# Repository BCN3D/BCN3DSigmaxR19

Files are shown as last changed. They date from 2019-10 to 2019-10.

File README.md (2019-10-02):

## What’s hold in this repository?
This repository will hold all the information about the Mechanics of the BCN3D Sigmax R19.
As a declared Open Source organization, it's in our mission to release all the original design files to you to be able to learn, reuse and improve. Open Source not only means code, it also concerns hardware.

We’ve managed to design and manufacture the BCN3D Sigmax R19 thanks to our previous experience in the 3D printing industry, the ideas coming from the community, our engineering background and a narrow collaboration with our suppliers. Our goal is justify the decisions we took and share the know-how we acquired so far.

We also provide the source files for those who want to check the core of the BCN3D Sigmax R19. You can consult both the CAD files and the technical drawings.

## CONCEPT DESIGN
During the concept design stage we set a clear target which determined the whole design and decisions: The BCN3D Sigmax R19 is a professional printer.

### Aesthetics
It has to look  like a professional equipment. Our previous printers were made with aluminium extruded profiles and plastic printed parts. That made sense for printers oriented to makers or schools, sold as a kit. But, in this case, aesthetic was a major player. For this reason, we adopted a welded aluminium frame, which allows the Sigmax to be a unique and attractive 3D printer

### Multimaterial
As a professional printer, it has to print as many materials as possible. Not only for engineers, who require tough -or flexible-, functional polymers, but also for designers who need the aesthetic component. However, material is not the only limitation. Complex geometries, overhangs and 3D printing doesn’t get along. So we wanted the Sigmax to be a real solution for those users who need to print with supports as a must. In conclusion, the Sigmax is the first and only commercial 3D printer with an Independent Dual Extuder (IDEX) system, which avoid all the side problems dual extrusion may cause.

### High Quality
The 3D Printing industry is maturing. Users are more and more demanding and 3D printing must be a solution, not a headache. For this reason, the Sigmax has to be a reliable piece of engineering, easy to assemble, maintain and capable to print seamlessly high quality objects, no matter how complex they are.

### High Capacity
Real-life and functional parts are not always small. A big printing volume is a great advantage for a professional 3D Printer although the Sigmax intends to be a desktop-sized printer. Allocating all the items and devices inside the frame, while granting ease-to-use and optimizing the axes structure were a key goal.

## DETAIL DESIGN INSIGHTS

We faced dozens of challenges during the design process. Below we describe some of them:

### Frame
Probably the biggest challenge. First we thought in a chassis made of profiles and then cover it. But then realized the cost in materials for that solution would be high enough to look for alternatives that could contribute more in the aesthetic field, even that could be a bit more expensive. On the other side, we wanted the Sigmax to be an accessible printer, wide and open in order to ease the handling and operation. So we decided to explore the option of designing a unibody frame where all the mechanical components were mounted on and with a wide frontal oberture.

First we had to decide between using aluminium or steel. Steel offers many advantages: It’s a very stiff metal, great to build structures and precise mechanical systems. In addition, it’s easy to work with and cheap. But it’s -really- heavy. We contemplated the option of using a thinner metal sheet of steel for the frame. After ordering a prototype, we dismissed the idea, though. Still it had a great mechanical behaviour and a relative low weight, the feeling of touching a thin metal sheet (1.5mm) was unpleasant because it felt like a cutting edge. And it didn’t look sturdy. So to achieve both a reliable look and a pleasant contact, we needed to go up to 3mm thickness. But then the shipping costs would be absurdly high and the handling, a constant hassle -both during the assembly process and for the final user.

Aluminium, on the other hand, provides lightness and a smooth and sturdy look. But it’s more expensive as a material and it’s harder to laser cut and weld. After balancing pros and cons, we bet on aluminium option -although we had a plan B.

The second big issue to manage was the manufacturing process. We contemplated two different ways to do it: either manufacture the frame by parts and screw them all together in the assembly line or weld the frame. Welding aluminium is hard and the welding process itself has some thermal and geometric implications that have to be considered. But it allows to reduce the assembling time dramatically while it outsources a key process.

As alternative, designing the frame as separate parts to screw together was considerably cheaper - as you save a handmade process such as welding and polishing. But the assembling of the frame and adjustment could be very delicate and incompatible with our production tag time. So the overall cost wouldn’t be that different in both options. The aesthetic component, though, would be very penalized with this alternative, because we would need to add dozens of screws on the frame.

For these reasons, we finally opted for a welded structure. We sat hours with our supplier discussing the best way to design every single part in order to grant a proper alignment between the faces that would hold the axes. Furthermore, we also studied the mechanical behaviour of the frame with some CAE studies, simulating stress and deformations during a standard usage.

### High quality components
A good frame is not enough to achieve amazing results. In such a precision equipment as the Sigmax, all the mechanical components play a key role. Due to the product requirements in terms of size and use of the internal space of the printer we had, we opted for a axes structure with the toolheads moving in the XY plane and an up and down moving Z axis.

With the XY plane decided to mount high precision linear guides. Despite its cost slightly higher than a system based on rods and bearings, the linear rails offer a professional look, an easy assembling and a compact package.

Regarding the Z axis, we were aware of the importance to have a robust guide system in order to avoid classic artifacts in printed parts related with a bad Z performance, such as Z wobbling. We also had experience using couplings and to connect the actuator with the leadscrew and we knew that a bad assembling could cause poor quality results. With this background, we chose using Ø12mm guide rods and a stepper motor with an inserted leadscrew. The whole system provides a high repeatability and accuracy.

### Independent Dual Extrusion
A 3D printer with such an specific feature increases the design unknowns and multiplies the components. Not only the firmware and the electronics need to be highly customized, but also mechanically there are some decisions to take.

First of all, because of the multiple components to hold, the internal parts tend to be more complex than other printers. So we decided to use aluminium sheet bending technology to manufacture the inner parts. As the manufacturing tolerances are acceptable for the purposes we intend and the technology is cheap and easily scalable, we considered the technology optimum.  

Two independent Extruders means have an extra moving stepper for the second toolhead, and the extra toolhead itself. On the other hand, when printing with both extruders it’s important to have a bucket to purge the idle hotends before start printing the model again. All this parts add weight to a moving element, which is a problem to print fast because the high inertias may worsen the print quality. So we designed the X and Y Axis as light as possible, saving as many grams as possible with every single component. Not only weight is important when doubling the toolheads, but also space. So we decided to adopt a bowden-based feeding system and miniaturize all the items as much as possible.

### Big Printing Volume
The BCN3D Sigmax R19 features 420x297x210mm printing volume. In order to provide such a big volume and a free space on both sides to park the idle toolhead, but still having a desktop-sized printer, we had to reorient the Z platform. The main issue to solve, though, was granting the stiffness of the structure with a big overhang of more than 300mm.

To prevent vibrations, we adopted high quality bearings with low clearance and we designed and  simulated a custom metal sheet structure, which allows to get a great quality prints with a smooth surface despite the big overhang.

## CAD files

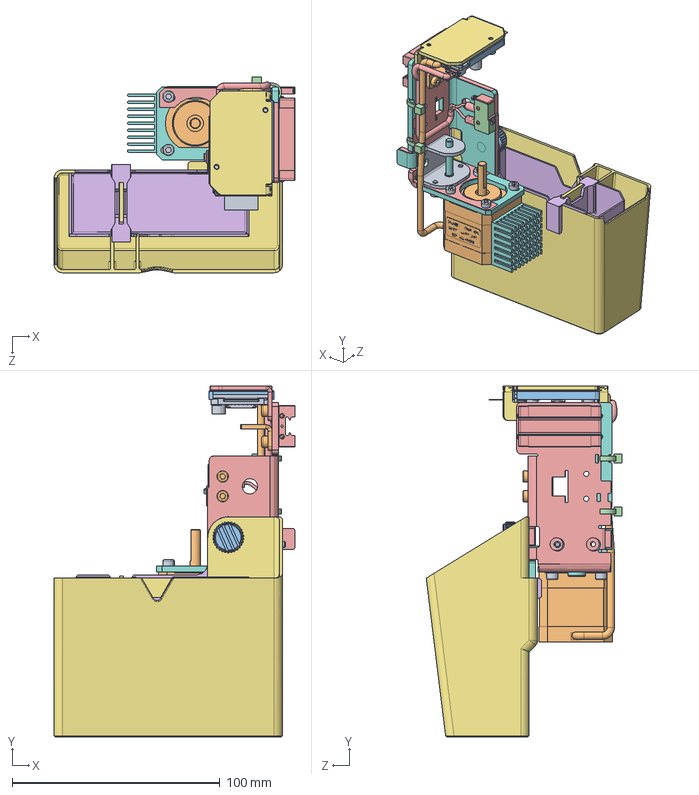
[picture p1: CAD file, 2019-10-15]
CAD/SW/BCN3DSigma-M05C02.0P000 X Axis Right.SLDASM
116.0 x 169.0 x 94.2 mm
DIN912 M3x6 x 8
DIN912 M3x8 x 6
DIN125 M3 poliamida x 2
DIN125 M3 x 2
10850-B00_Purger base right
040M05C02.0P04B X Stepper Driver Holder Right
BCN3DSigma-M02C01.0P10A Idler pulley shaft
BCN3DSigma-M04C00.0P03F Stepper Driver Board
10901-A00_Nema 14
BCN3DSigma-M05C01.0P08Z Purger Button
BCN3DSigma-M09C00.0P20A Zip tie x 2
Linear guide slide
Sigma_R17-M05C01.0P14D Cloth Support
BCN3DSigma-M05C01.0P07C Silicone Cloth
10828-A00_Stepper Holder Right
10830-B01_X Axis Idler
BCN3DSigma-M05C01.0P01D Belt Clamp
BCN3DSigma-M05C01.0P11F Driver spacer
BCN3DSigma-M02C01.0P08Z Endstop
BCN3DSigma-M09C00.0P15A Endstop X Right
BCN3DSigma-M04C00.0P09A Drivers Heatsink
040M05C01.0P017Z Heatsink 28x28x15

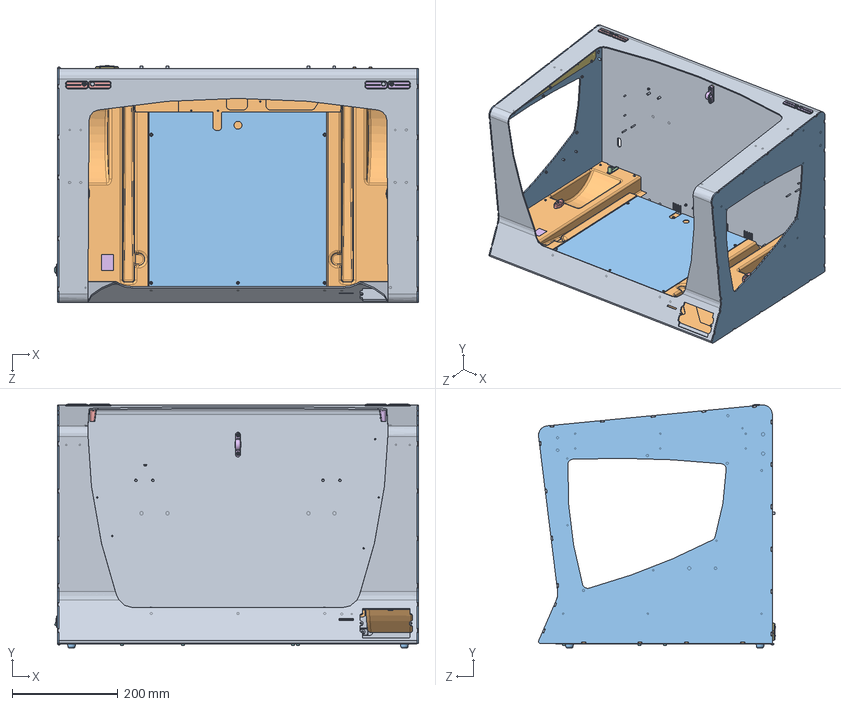
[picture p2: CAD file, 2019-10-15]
CAD/SW/040M01C00.0P000 Structure.SLDASM
686.9 x 459.6 x 447.2 mm
040M01C01.0P01K (RiT - Reverse Engineered) Top frame
040M01C01.0P02E (Test) Bottom frame
BCN3DSigma-M01C01.0P03D (Test) Left_Right side x 2
BCN3DSigma-M01C01.0P05D Y Idler Tensioner x 2
BCN3DSigma-M01C01.0P29H Bowden exit Left
BCN3DSigma-M01C01.0P29H Bowden exit Right
BCN3DSigma-M01C01.0P07G (Test) Guide spacer x 2
040M01C01.0P11Z Power button
040M01C01.0P12Z USB Extension Cable
040M01C01.0P15A Square 90 x 8
040M01C01.0P16A Square 60 x 3
BCN3DSigma-M01C01.0P30C Curve flat cable holder x 2
BCN3DSigma-M01C01.0P20C Front LED connector clamp x 2
BCN3DSigma-M01C01.0P22D Plain flat cable holder x 4
040M04C00.0P07Z Power Entry Filter
040M01C01.0P17Z Fusible
DIN7982 M3.5x13 x 2
A3DIN912 M3x10 x 6
A3DIN125 M3 poliamida x 14
A3DIN934 M3 x 48
A3DIN985 M3 x 9
040M02C01.0P14A DRY-RUNNING MOUNTED SLEEVE BRNG
040M02C01.0P15C Y Axis Pillow Bearing Spacer
A3DIN7981 3.2x9.5 x 6
A3ISO7380 M3x10 x 11
040M01C02.0P01E Inner cover
BCN3DSigma-M01C02.0P06D Bowden entry guide x 2
BCN3DSigma-M01C02.P07F Bowden entry x 2
040M01C02.0P09A Crush Label
10924-A00_Coupling collet x 2
A3DIN912 M3x6 x 7
A3DIN125 M3 x 4
14062-A00_Bottom cover
040M01C03.0P02Z Leg x 4

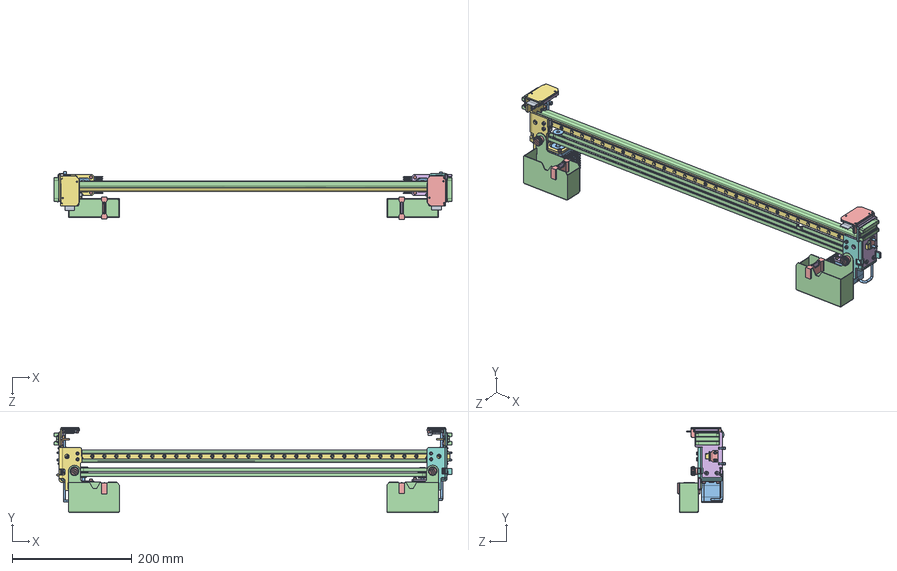
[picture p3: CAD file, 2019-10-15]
CAD/SW/040M05C00.0P000 X Axis.SLDASM
663.4 x 142.0 x 79.4 mm
BCN3DSigma-M02C01.0P15Z GT2 Pulley Ø4 Bearing Bore 6 Runice x 2
BCN3DSigma-M02C01.0P016Z Spacer 4x8x6 Essentra x 2
BCN3DSigma-M05C01.0P15Z GT2 Pulley Ø5 Bore 6 Runice x 2
040M05C00.0P01Z X Belt x 2
DIN912 M3x6 x 16
DIN912 M3x8 x 12
DIN912 M3x10 x 2
DIN125 M3 poliamida x 4
DIN125 M3 x 4
10831-A00_Belt Clamp
10901-A00_Nema 14 x 2
10849-B00_Purger base left
BCN3DSigma-M05C01.0P08Z Purger Button x 2
BCN3DSigma-M05C01.0P11F Driver spacer x 2
BCN3DSigma-M05C01.0P12B X Stepper Driver Holder Left
BCN3DSigma-M02C01.0P10A Idler pulley shaft x 2
BCN3DSigma-M04C00.0P03F Stepper Driver Board x 2
BCN3DSigma-M09C00.0P15A Endstop X Left
BCN3DSigma-M09C00.0P20A Zip tie x 4
Linear guide slide x 2
Sigma_R17-M05C01.0P14D Cloth Support x 2
BCN3DSigma-M05C01.0P07C Silicone Cloth x 2
10028-A00_Stepper Holder Left
10830-B01_X Axis Idler x 2
BCN3DSigma-M02C01.0P08Z Endstop x 2
BCN3DSigma-M04C00.0P09A Drivers Heatsink x 2
040M05C01.0P017Z Heatsink 28x28x15 x 2
10850-B00_Purger base right
040M05C02.0P04B X Stepper Driver Holder Right
10828-A00_Stepper Holder Right
BCN3DSigma-M05C01.0P01D Belt Clamp
BCN3DSigma-M09C00.0P15A Endstop X Right
A3DIN912 M3x6 x 4
A3DIN912 M3x10 x 4
A3DIN912 M3x8 x 6
14060-A00_X Reinforcement x 2
BCN3DSigma-M05C03.0P02G X Support x 2
10847-A01_connection plate x 3
14068-A00_X Guide

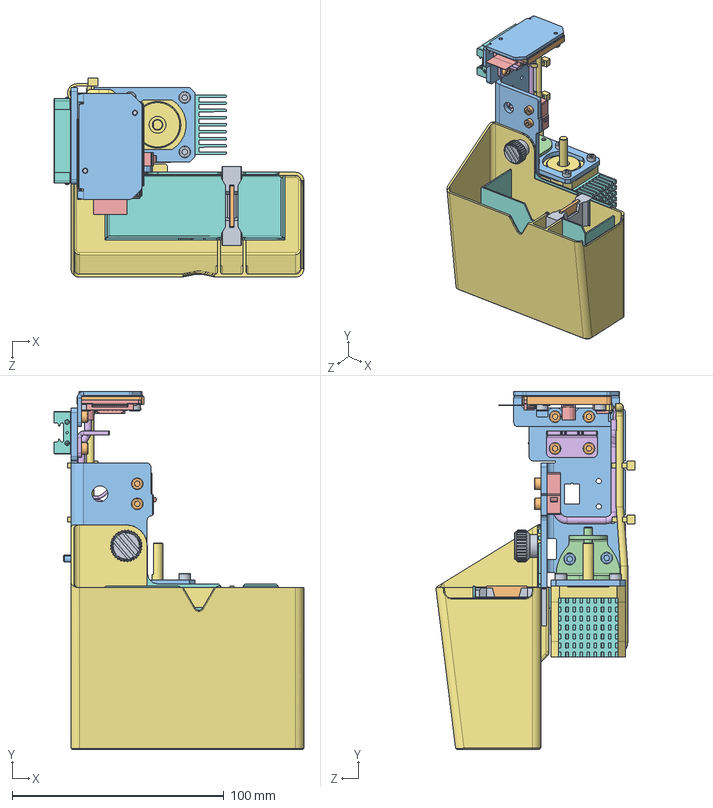
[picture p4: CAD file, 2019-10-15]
CAD/SW/BCN3DSigma-M05C01.0P000 X Axis Left.SLDASM
118.0 x 169.0 x 94.2 mm
DIN912 M3x6 x 8
DIN912 M3x8 x 6
DIN912 M3x10 x 2
DIN125 M3 poliamida x 2
DIN125 M3 x 2
10831-A00_Belt Clamp
10901-A00_Nema 14
10849-B00_Purger base left
BCN3DSigma-M05C01.0P08Z Purger Button
BCN3DSigma-M05C01.0P11F Driver spacer
BCN3DSigma-M05C01.0P12B X Stepper Driver Holder Left
BCN3DSigma-M02C01.0P10A Idler pulley shaft
BCN3DSigma-M04C00.0P03F Stepper Driver Board
BCN3DSigma-M09C00.0P15A Endstop X Left
BCN3DSigma-M09C00.0P20A Zip tie x 2
Linear guide slide
Sigma_R17-M05C01.0P14D Cloth Support
BCN3DSigma-M05C01.0P07C Silicone Cloth
10028-A00_Stepper Holder Left
10830-B01_X Axis Idler
BCN3DSigma-M02C01.0P08Z Endstop
BCN3DSigma-M04C00.0P09A Drivers Heatsink
040M05C01.0P017Z Heatsink 28x28x15

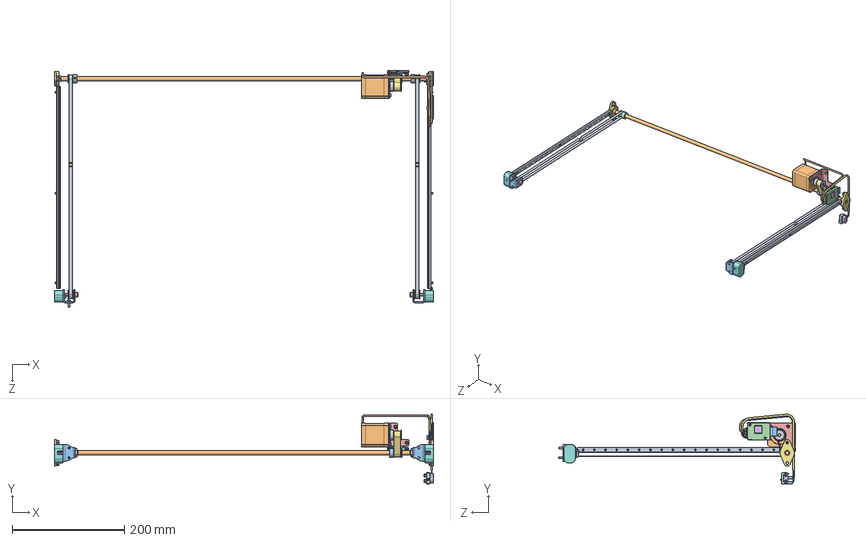
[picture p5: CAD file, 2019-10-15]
CAD/SW/040M02C00.0P000 Y Axis.SLDASM
675.5 x 124.6 x 421.8 mm
A3DIN985 M2.5 x 2
A3DIN912 M3x6 x 6
A3DIN912 M3x10 x 11
A3DIN913 M3x3 x 4
A3DIN934 M5 x 4
A3DIN913 M4x3 x 4
040M02C01.0P01Z Bearing Pillow Block x 2
BCN3DSigma-M02C01.0P02E Idler Spacer x 2
040M02C01.0P03Z Y Guide x 2
14065-A00_Transmission Bar
10838_A01-Y Axis Idler x 2
040M02C01.0P08Z Endstop
BCN3DSigma-M02C01.0P10A Idler pulley shaft x 2
BCN3DSigma-M02C01.0P12A Y Endstop spacer
040M09C00.0P14B Y Endstop cable
040M09C00.0P21A Enstop shrink tube x 2
040M02C01.0P09Z Y Belt x 2
BCN3DSigma-M02C01.0P15Z GT2 Pulley Ø4 Bearing Bore 6 Runice x 2
10883-A00_Pulley Ø8 Bore 12 Runice
10885-A00_GT2 Pulley Ø8 Bore 6 Runice x 2
A3DIN934 M3 x 6
A3DIN 913 M3x10 x 2
A3DIN125 M3 poliamida x 2
040M02C02.0P02C Y Belt tensor
040M02C02.0P04Z GT2 Pulley Ø5mm Bore 12mm width
040M02C02.0P06Z Nema17 47mm
040M04C00.0P03F Stepper Driver Board
BCN3DSigma-M05C01.0P11F Driver spacer
040M02C02.0P01D Y Stepper Holder
Drivers Heatsink
040M02C00.0P01Z Y Main Belt

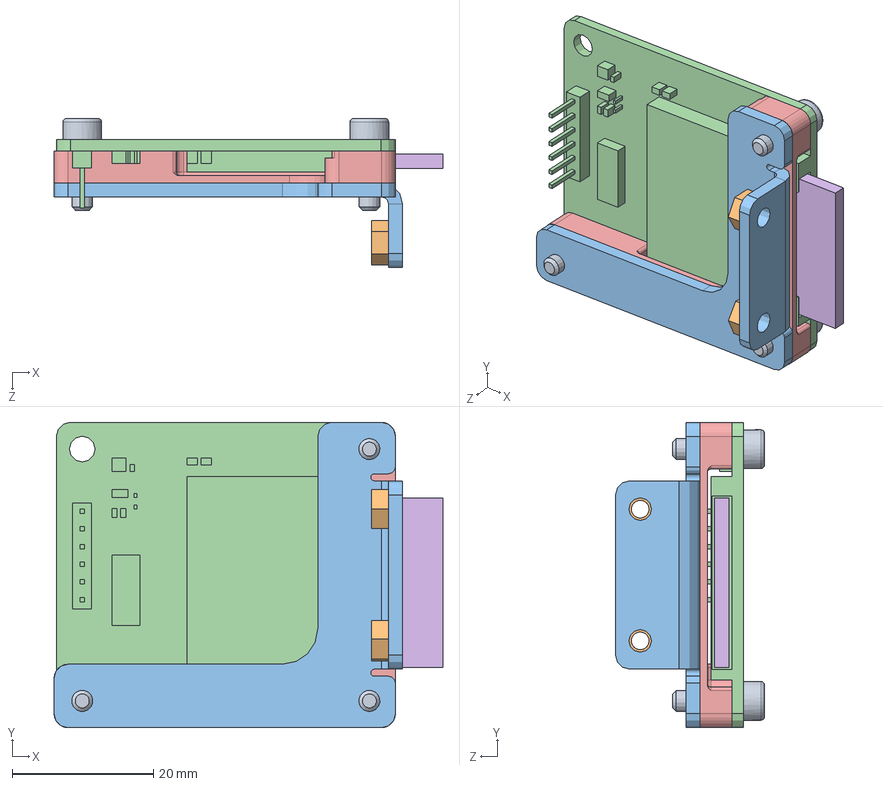
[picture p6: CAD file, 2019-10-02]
CAD/SW/040M04C02.0P000 SD Unit.SLDASM
55.1 x 43.2 x 21.1 mm
A3DIN912 M3x10 x 3
A3DIN934 M3 x 2
040M04C02.0P01D SD Holder
BCN3DSigma-M04C02.0P02AA SD module
040M04C02.0P03A SD spacer
040M04C02.0P04Z SD Card 8GB

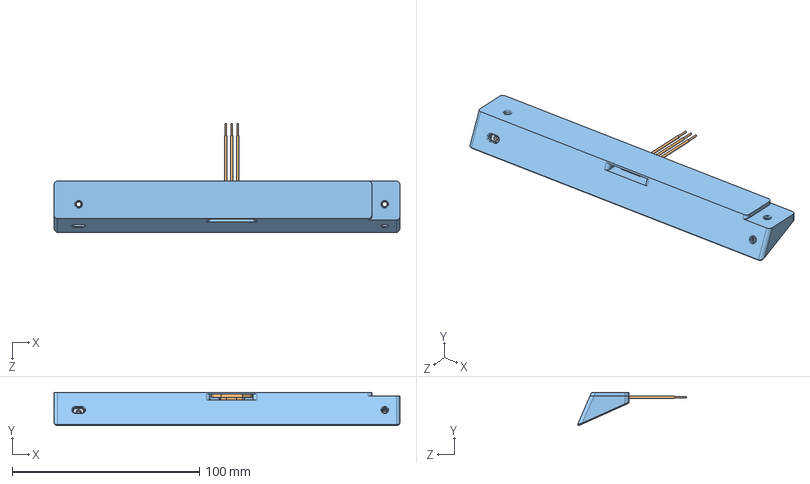
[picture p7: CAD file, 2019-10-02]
CAD/SW/040M01C04P000 HES Mount.SLDASM
185.0 x 17.9 x 58.2 mm
DIN934 M3 x 4
NPN Hall Effect Sensor (RS=765-9325)
040M01C04P002B Sensor Mount

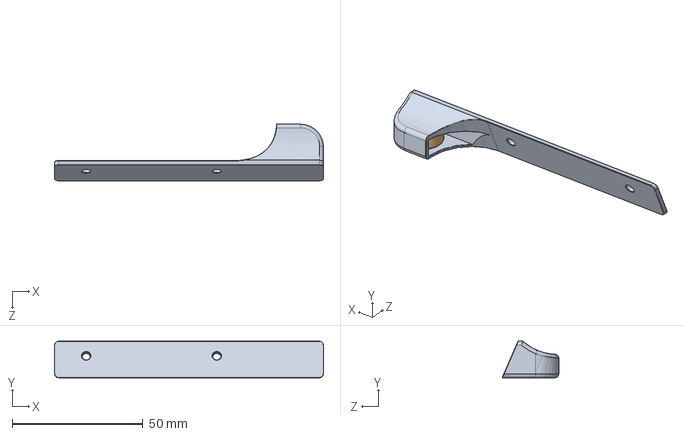
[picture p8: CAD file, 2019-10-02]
CAD/SW/040M01C04P001 HES Trigger.SLDASM
103.0 x 14.0 x 21.7 mm
040M01C04P003E Magnet Holder
Magnet (Supermagnete = R-15-06-06-N)

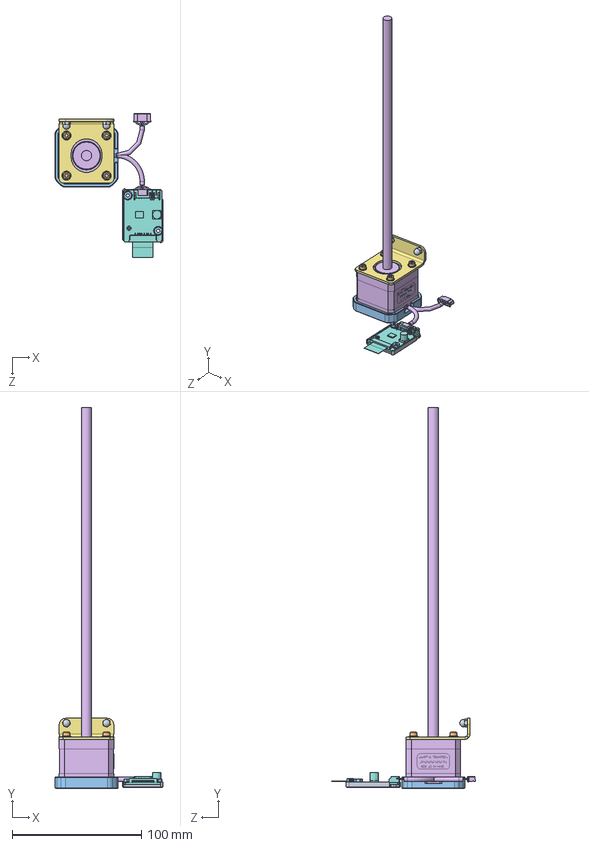
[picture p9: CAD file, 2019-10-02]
CAD/SW/040M03C03.0P000 Z Motor.SLDASM
83.6 x 294.5 x 111.5 mm
A3DIN1587 M3 x 2
A3DIN912 M3x10 x 4
A3DIN934 M3 x 2
A3DIN125 M3 x 4
A3DIN125 M3 poliamida x 2
040M03C03.0P01Z Z Motor
BCN3DSigma-M03C03.0P02C Z Stepper Holder
040M04C00.0P03F Stepper Driver Board
BCN3DSigma-M05C01.0P11F Driver spacer
Drivers Heatsink
Z Motor Rest Support^040M03C03.0P000 Z Motor

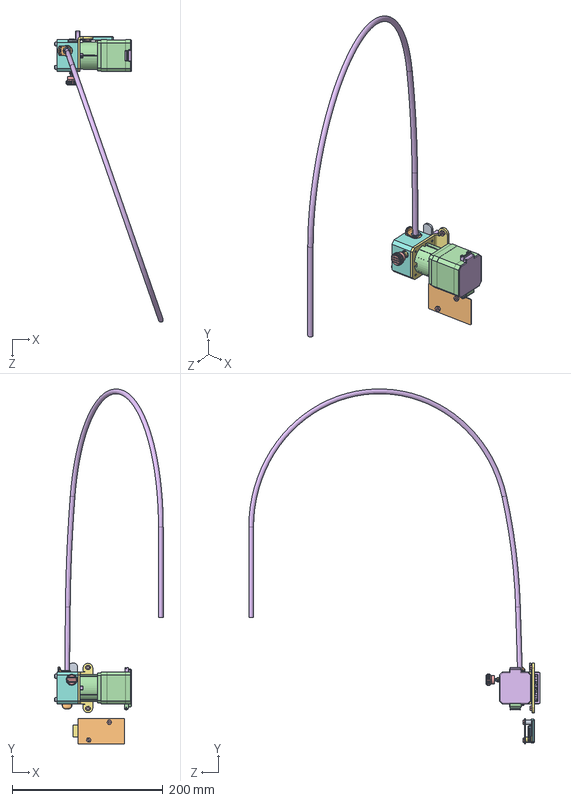
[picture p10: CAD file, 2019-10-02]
CAD/SW/040M07C01.0P000C Left extruder.SLDASM
143.8 x 470.5 x 386.3 mm
A3DIN912 M3x30 x 3
A3DIN913 M3x3
DIN931 M4x50 (91280A154)
A3DIN912 M3x8 x 3
A3DIN934 M3 x 4
040M07C01.0P29B (Test) Separador Drive Gear
040M04C00.0P03F Stepper Driver Board
BCN3DSigma-M05C01.0P11F Driver spacer
Separador nylon negre 3.2x6x8 x 2
040M07C01.0P06C Extruder driver cover
PHR-6_PRUEBA x 2
040M07C01.0P10AA Nema 17 40mm
040M07C01.0P25Z Driving Gear
040M07C01.0P24Z Driven Gear
040M07C01.0P05E Extruder Stepper Holder
040M07C01.0P026E Extruder Body Left
040M07C01.0P027B Extruder Tensor Left
040M07C01.0P04D Pneufit coupling x 2
040M07C01.0P19Z Coupling collet x 2
040M07C01.0P029Z Pin
040M05C01.0P08Z Purger Button
040M07C01.0P07B Bowden tube
040M07C01.0P13A Extruder spring
Drivers Heatsink
filament
BCN3DSigma-M07C01.0P14D Coupling Clip x 2

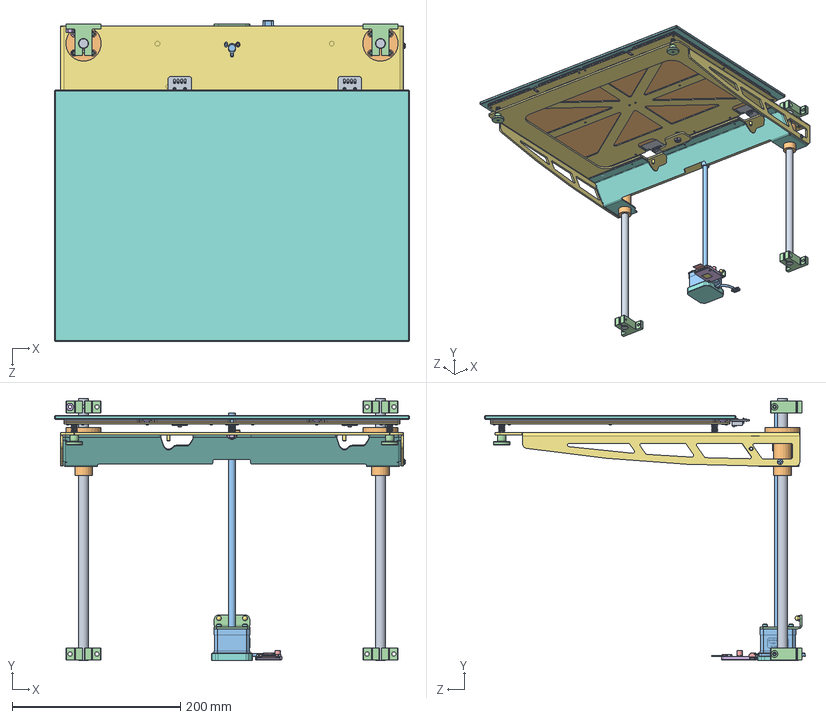
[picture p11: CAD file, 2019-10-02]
CAD/SW/040M03C00.0P000 Z axis.SLDASM
422.0 x 312.0 x 381.5 mm
040M03C01.0P01G Lower platform
040M03C01.0P02E Reinforcement
040M03C01.0P03B Z Bar x 2
040M03C01.0P04Z Flanged Linear Bushing x 2
040M03C01.0P06Z Shaft Support x 4
A3DIN7991 M3x6 x 18
A3DIN985 M5
040M03C02.0P01D Upper platform
14066-A00_Glass
040M03C02.0P05E Heated bed x 2
040M03C02.0P03C Cork x 2
040M03C02.0P04Z Printing surface spring x 3
040M03C02.0P07Z Bed Thumbscrew x 2
040M03C02.0P09A Thumbscrew Label x 2
040M03C02.0P06Z Magnet x 4
A3DIN1587 M3 x 2
A3DIN912 M3x10 x 4
A3DIN934 M3 x 2
A3DIN125 M3 x 4
A3DIN125 M3 poliamida x 2
040M03C03.0P01Z Z Motor
BCN3DSigma-M03C03.0P02C Z Stepper Holder
040M04C00.0P03F Stepper Driver Board
BCN3DSigma-M05C01.0P11F Driver spacer
Drivers Heatsink
Z Motor Rest Support^040M03C03.0P000 Z Motor

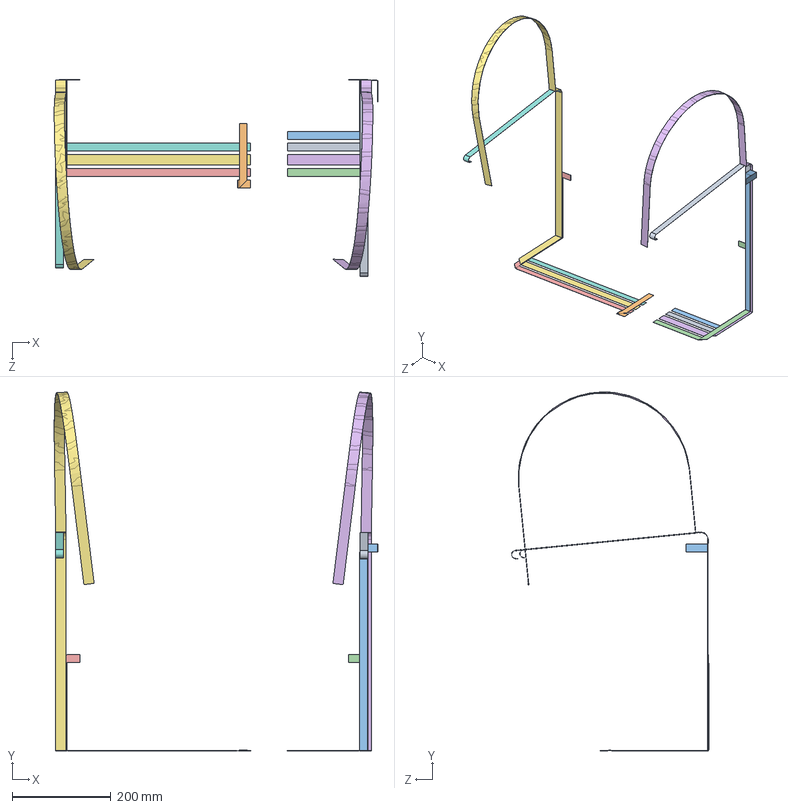
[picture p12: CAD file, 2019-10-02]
CAD/SW/040M09C00.0P000 Wiring.SLDASM
656.3 x 728.0 x 399.5 mm
040M09C00.0P01A FFC X1 stepper
040M09C00.0P03A FFC Z stepper
040M09C00.0P04A FFC Y stepper
040M09C00.0P05A FFC Extruder 1
040M09C00.0P06B FFC Extruder 0
040M09C00.0P08B FFC Hotend 1
040M09C00.0P07C FFC Hotend 0
040M09C00.0P02B FFC X0 stepper

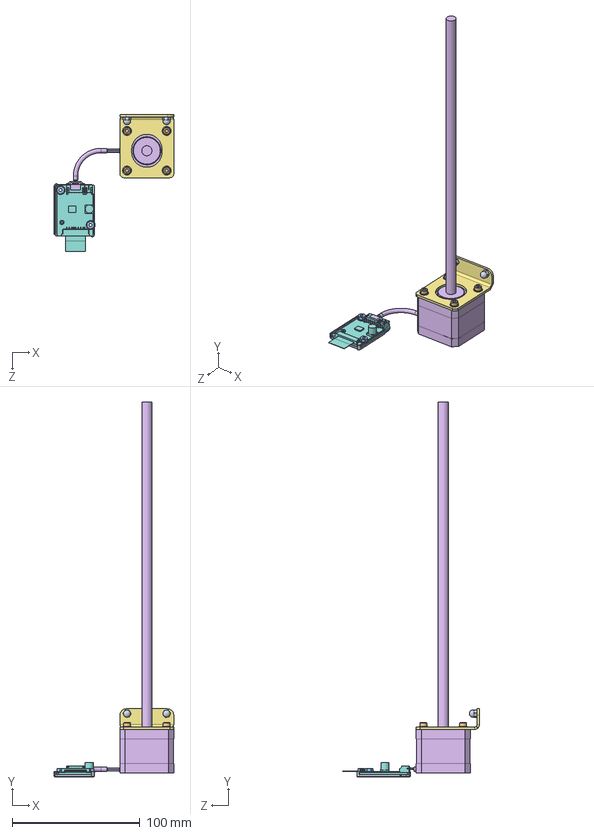
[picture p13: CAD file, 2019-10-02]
CAD/SW/BCN3DSigma-M03C03.0P000 Z Motor.SLDASM
93.8 x 293.6 x 107.2 mm
DIN1587 M3 x 2
DIN912 M3x10 x 4
DIN934 M3 x 2
DIN125 M3 x 4
DIN125 M3 poliamida x 2
10903-A00 Z Motor
10983-A00_Z Stepper Holder
BCN3DSigma-M04C00.0P03F Stepper Driver Board
BCN3DSigma-M05C01.0P11F Driver spacer
BCN3DSigma-M04C00.0P09A Drivers Heatsink

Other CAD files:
CAD/SW/040M07C04.0P000 Filament Runout Sensor.SLDASM
CAD/SW/040M04C01.0P02A Cable mainboard to adapator lcd.sldasm
CAD/SW/040M07C03.0P000 Bifurcation.sldasm
CAD/SW/040M05C01.0P000 X Axis Left.SLDASM
CAD/SW/040M09C00.0P17B Relay to mainboard cable.sldasm
CAD/SW/040M01C01.0P11Z Power button.SLDPRT
CAD/SW/040M01C01.0P12Z USB Extension Cable.SLDPRT
CAD/SW/040M01C01.0P15A Square 90.SLDPRT
CAD/SW/040M01C01.0P16A Square 60.SLDPRT
CAD/SW/040M01C01.0P17Z Fusible.SLDPRT
CAD/SW/040M01C02.0P000 Structure covers.SLDASM
CAD/SW/040M01C02.0P01E Inner cover.SLDPRT
CAD/SW/040M01C02.0P05F Extruder entry bowden.SLDPRT
CAD/SW/040M01C02.0P09A Crush Label.SLDPRT
CAD/SW/040M01C03.0P000 Bottom cover.SLDASM
CAD/SW/040M01C03.0P02Z Leg.SLDPRT
CAD/SW/040M01C04P002B Sensor Mount.SLDPRT
CAD/SW/040M01C04P003E Magnet Holder.SLDPRT
CAD/SW/040M02C01.0P14A DRY-RUNNING MOUNTED SLEEVE BRNG.SLDPRT
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

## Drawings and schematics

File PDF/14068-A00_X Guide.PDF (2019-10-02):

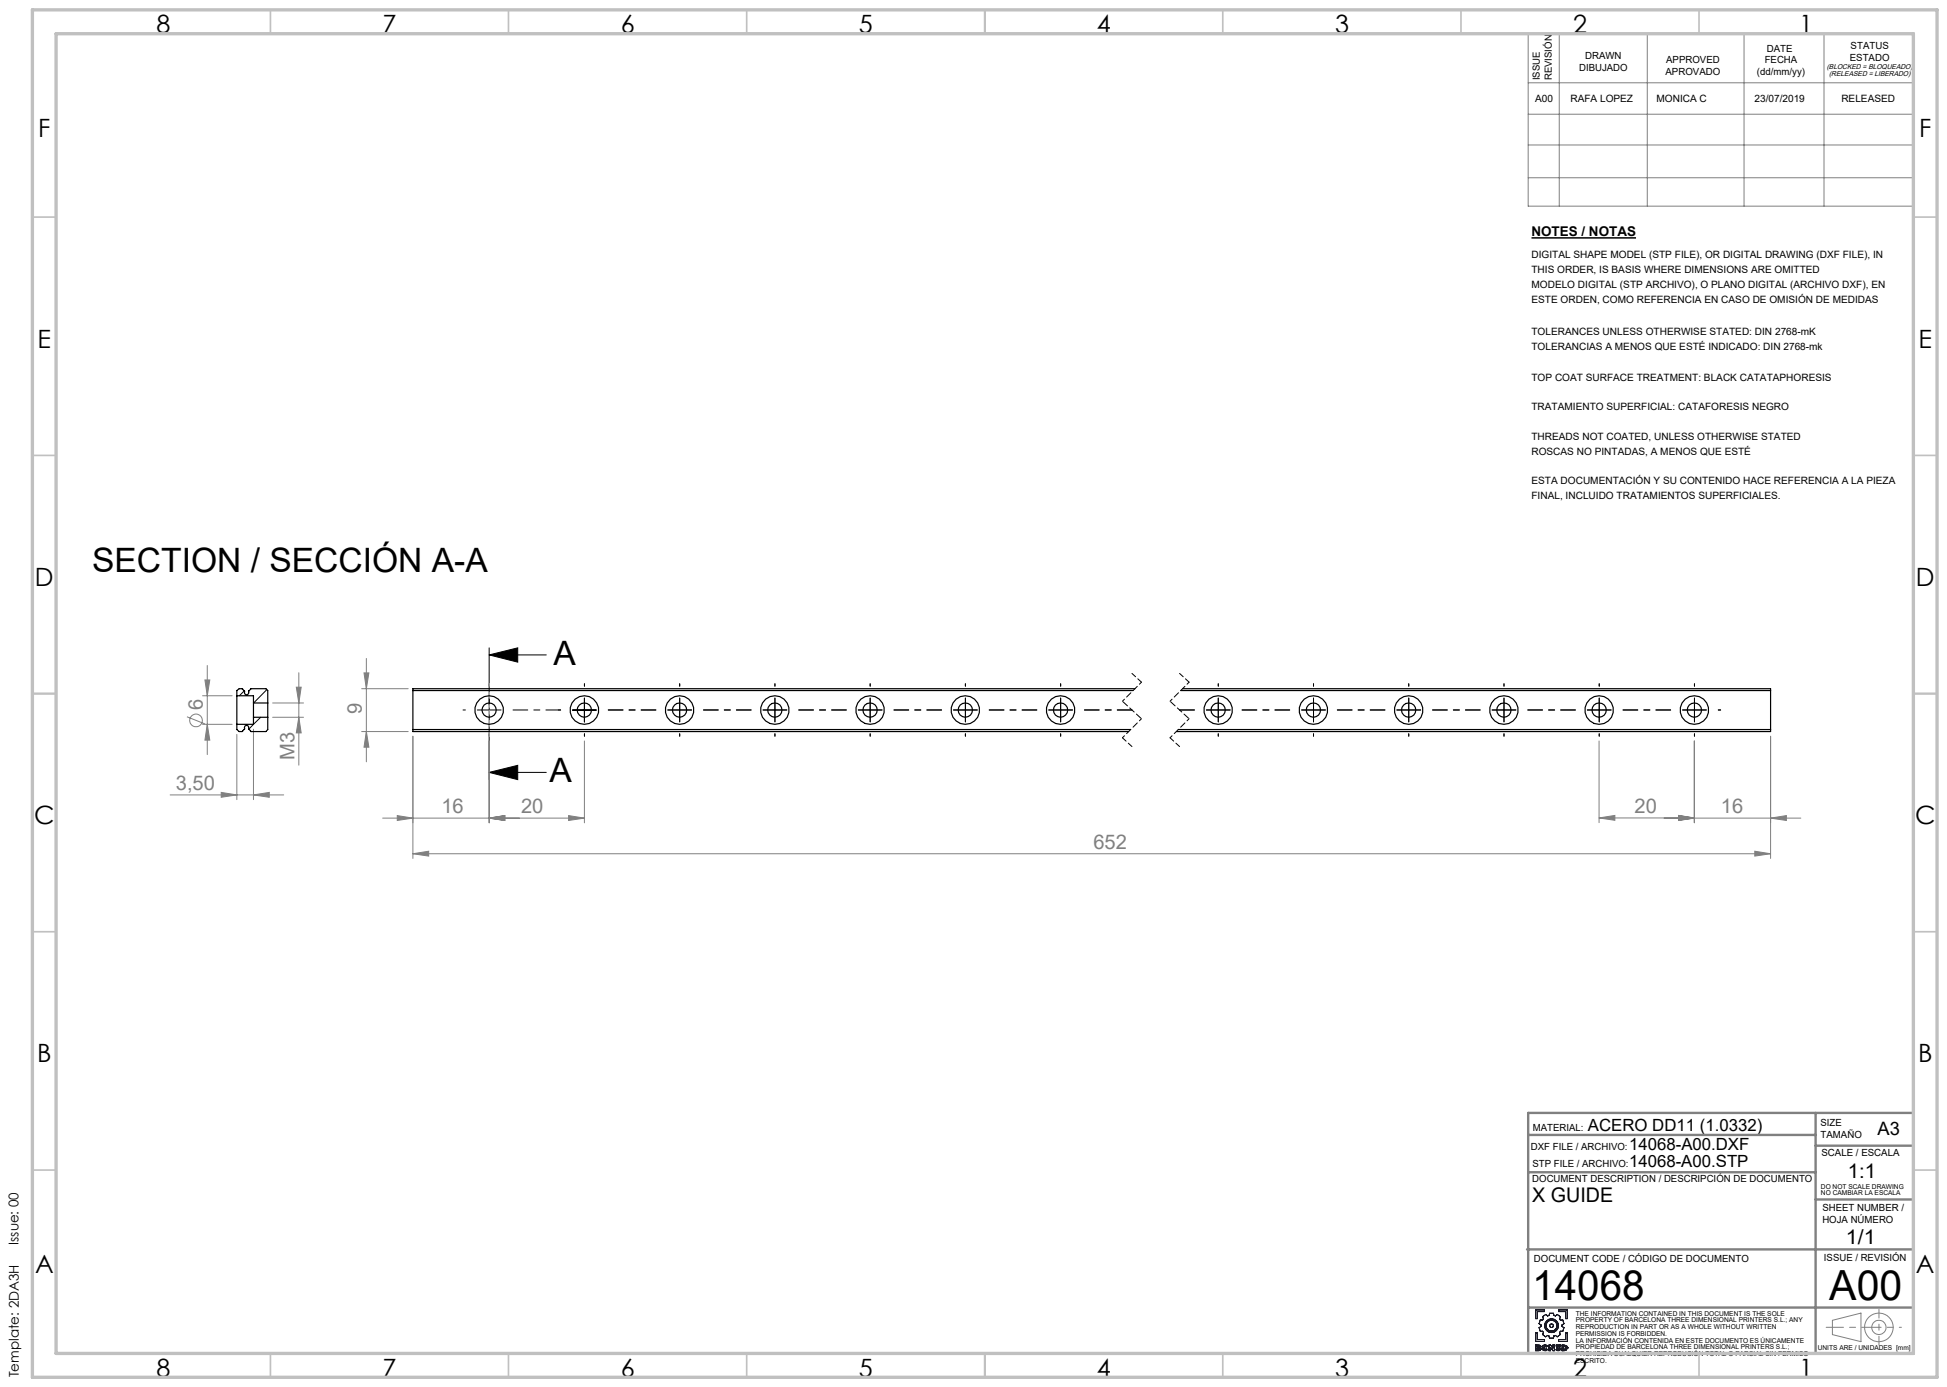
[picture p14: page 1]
SCALE / ESCALA; NOTES / NOTAS; SECTION / SECCIÓN A-A; Template: 2DA3H Issue: 00; ACERO DD11 (1.0332)

DRAWN DIBUJADO | APPROVED APROVADO | DATE FECHA (dd/mm/yy) | STATUS ESTADO (BLOCKED = BLOQUEADO) (RELEASED = LIBERADO)

A00 | RAFA LOPEZ | MONICA C | 23/07/2019 | RELEASED

DIGITAL SHAPE MODEL (STP FILE), OR DIGITAL DRAWING (DXF FILE), IN
THIS ORDER, IS BASIS WHERE DIMENSIONS ARE OMITTED
MODELO DIGITAL (STP ARCHIVO), O PLANO DIGITAL (ARCHIVO DXF), EN
ESTE ORDEN, COMO REFERENCIA EN CASO DE OMISIÓN DE MEDIDAS

TOLERANCES UNLESS OTHERWISE STATED: DIN 2768-mK
TOLERANCIAS A MENOS QUE ESTÉ INDICADO: DIN 2768-mk

TOP COAT SURFACE TREATMENT: BLACK CATATAPHORESIS

TRATAMIENTO SUPERFICIAL: CATAFORESIS NEGRO

THREADS NOT COATED, UNLESS OTHERWISE STATED
ROSCAS NO PINTADAS, A MENOS QUE ESTÉ

ESTA DOCUMENTACIÓN Y SU CONTENIDO HACE REFERENCIA A LA PIEZA
FINAL, INCLUIDO TRATAMIENTOS SUPERFICIALES.

MATERIAL:
DXF FILE / ARCHIVO:
STP FILE / ARCHIVO:
DOCUMENT DESCRIPTION / DESCRIPCIÓN DE DOCUMENTO
X GUIDE

DO NOT SCALE DRAWING
NO CAMBIAR LA ESCALA
SHEET NUMBER /
HOJA NÚMERO

DOCUMENT CODE / CÓDIGO DE DOCUMENTO 14068 | ISSUE / REVISIÓN A00

THE INFORMATION CONTAINED IN THIS DOCUMENT IS THE SOLE PROPERTY OF BARCELONA THREE DIMENSIONAL PRINTERS S.L.; ANY REPRODUCTION IN PART OR AS A WHOLE WITHOUT WRITTEN PERMISSION IS FORBIDDEN. LA INFORMACIÓN CONTENIDA EN ESTE DOCUMENTO ES ÚNICAMENTE PROPIEDAD DE BARCELONA THREE DIMENSIONAL PRINTERS S.L.; | UNITS ARE / UNIDADES [mm]

PROHIBIDA CUALQUIER REPRODUCIÓN TOTAL O PARCIAL SIN PERMISO
ESCRITO.

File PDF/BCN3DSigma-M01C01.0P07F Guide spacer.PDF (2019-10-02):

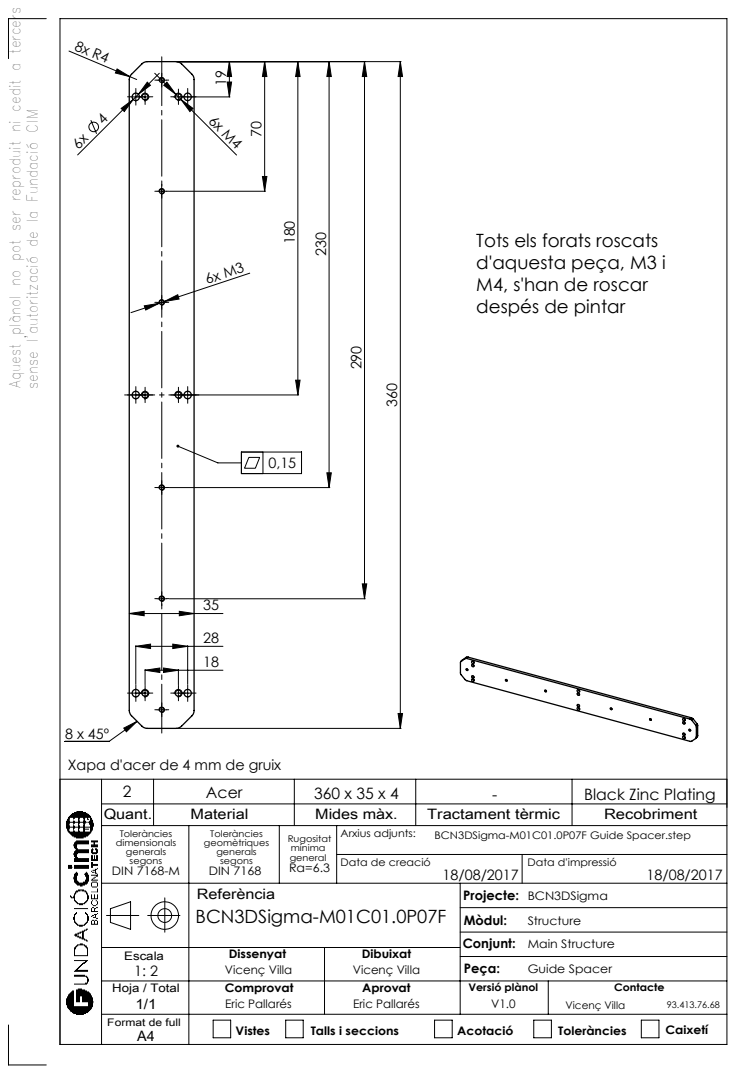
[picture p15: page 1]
Mides màx.; Tractament tèrmic; Recobriment; Data de creació; Data d'impressió; Vistes; Talls i seccions; Acotació; Toleràncies; Caixetí; Guide Spacer

Aquest plànol no pot ser reproduit ni cedit a tercers

sense l'autorització de la Fundació CIM

Tots els forats roscats
d'aquesta peça, M3 i
M4, s'han de roscar
despés de pintar

Xapa d'acer de 4 mm de gruix
Quant.

- Black Zinc Plating

Toleràncies dimensionals generals segons DIN 7168-M | Toleràncies geomètriques generals segons DIN 7168 | Rugositat mínima general Ra=6.3 | Arxius adjunts: BCN3DSigma-M01C01.0P07F Guide Spacer.step

Referència BCN3DSigma-M01C01.0P07F | Projecte: BCN3DSigma Mòdul: Structure Conjunt: Main Structure

Escala 1: 2 | Dissenyat Vicenç Villa | Dibuixat Vicenç Villa

Hoja / Total 1/1 | Comprovat Eric Pallarés | Aprovat Eric Pallarés | Versió plànol V1.0 | Contacte Vicenç Villa 93.413.76.68

Format de full A4

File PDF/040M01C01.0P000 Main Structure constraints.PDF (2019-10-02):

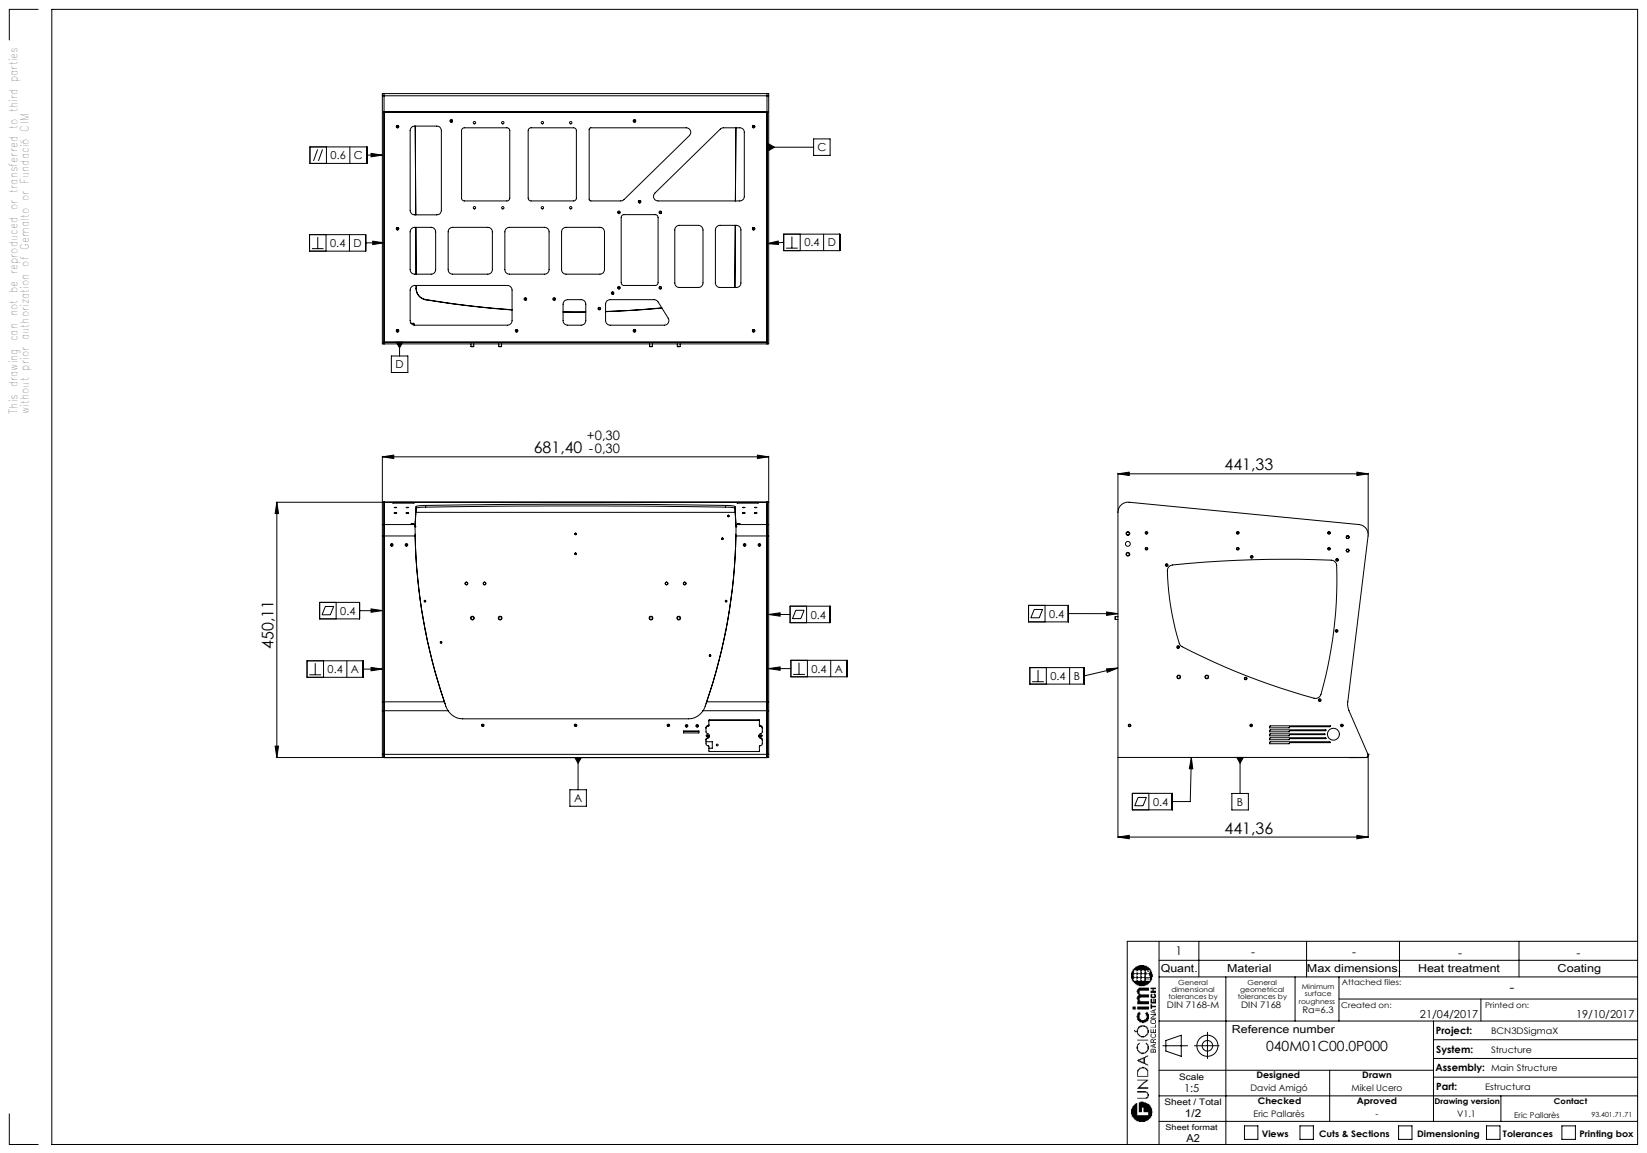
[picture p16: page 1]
Max dimensions.; Heat treatment; Coating; Created on:; Printed on:; Views; Cuts & Sections; Dimensioning; Tolerances; Printing box

This drawing can not be reproduced or transferred to third parties without prior authorization of Gemalto or Fundació CIM

General dimensional tolerances by DIN 7168-M | General geometrical tolerances by DIN 7168 | Minimum surface roughness Ra=6.3 | Attached files: | -

Reference number 040M01C00.0P000 | Project: BCN3DSigmaX System: Structure Assembly: Main Structure

Scale 1:5 | Designed David Amigó | Drawn Mikel Ucero

Sheet / Total 1/2 | Checked Eric Pallarès | Aproved - | Drawing version V1.1 | Contact Eric Pallarès 93.401.71.71

Sheet format A2

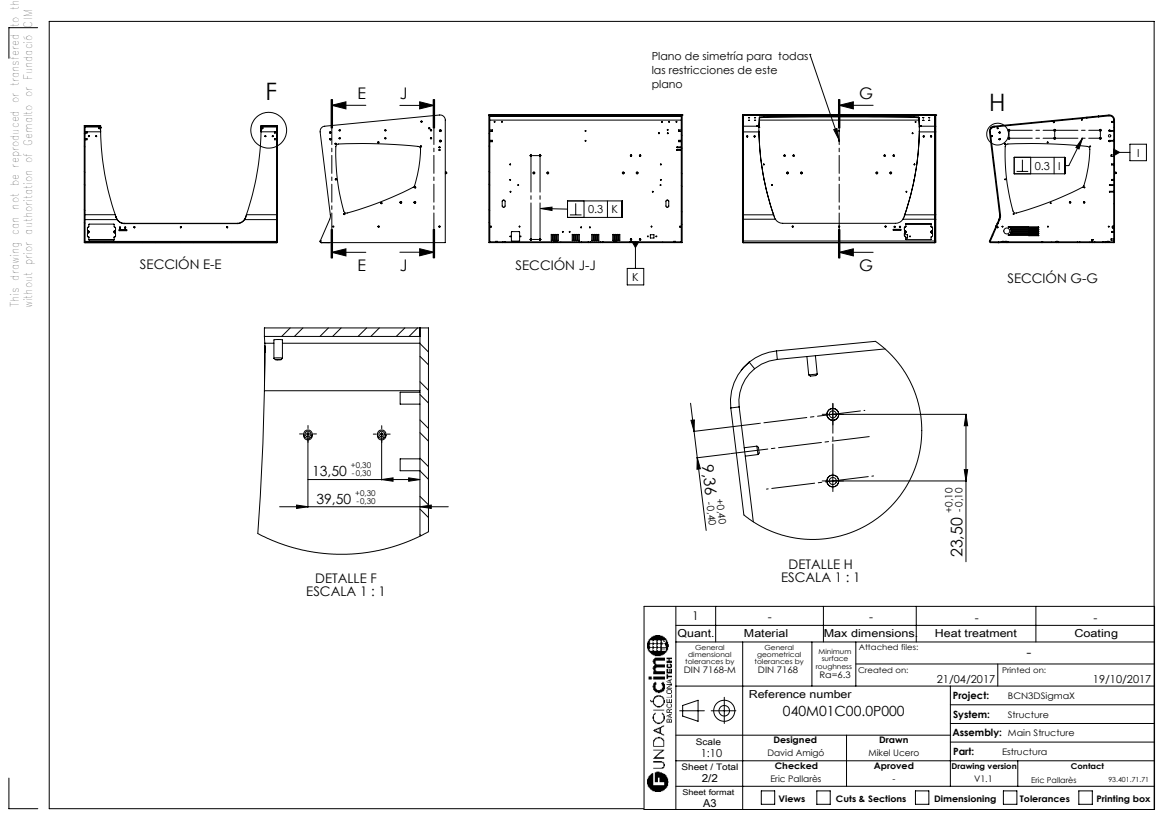
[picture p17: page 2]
Max dimensions.; Heat treatment; Coating; Created on:; Printed on:; Views; Cuts & Sections; Dimensioning; Tolerances; Printing box; SECCIÓN G-G; DETALLE H ESCALA 1 : 1; SECCIÓN E-E; DETALLE F ESCALA 1 : 1; SECCIÓN J-J

This drawing can not be reproduced or transfered to third parts

without prior authoritation of Gemalto or Fundació CIM

Plano de simetría para todas
las restricciones de este
plano

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

Reference number 040M01C00.0P000 | Project: BCN3DSigmaX System: Structure Assembly: Main Structure

Scale 1:10 | Designed David Amigó | Drawn Mikel Ucero

Sheet / Total 2/2 | Checked Eric Pallarès | Aproved - | Drawing version V1.1 | Contact Eric Pallarès 93.401.71.71

Sheet format A3

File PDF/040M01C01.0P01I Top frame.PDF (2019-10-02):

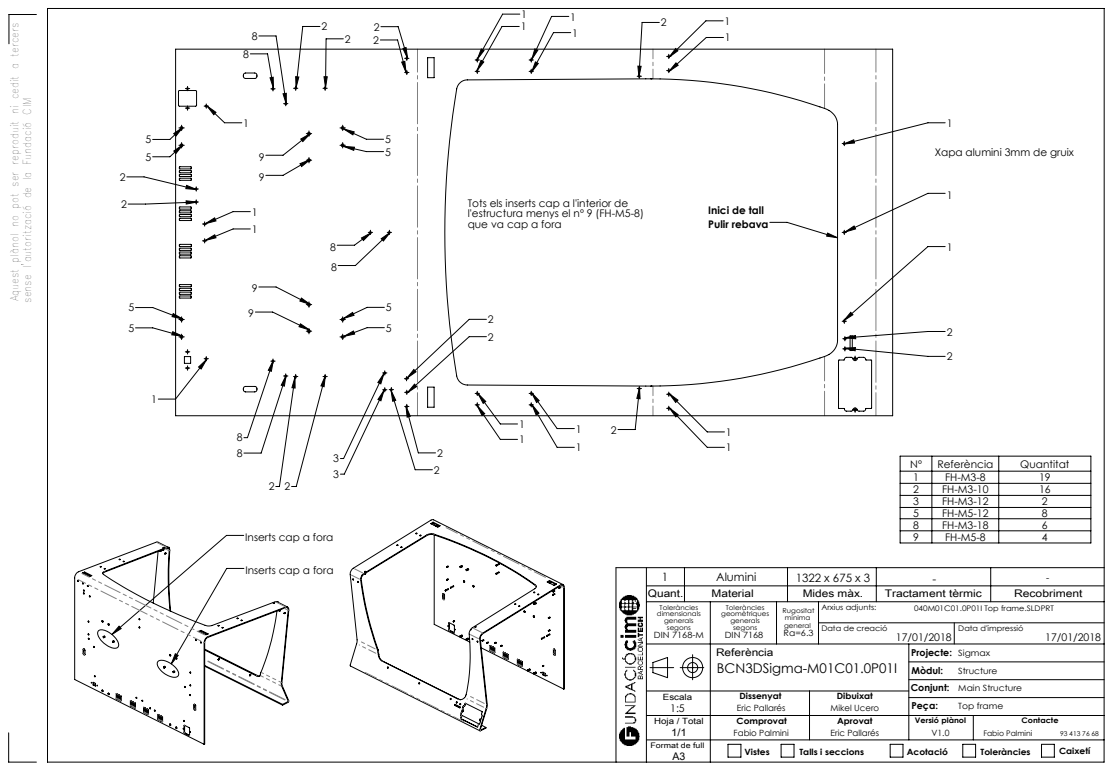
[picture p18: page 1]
Mides màx.; Tractament tèrmic; Recobriment; Data de creació; Data d'impressió; Vistes; Talls i seccions; Acotació; Toleràncies; Caixetí; Top frame; Referència; Quantitat 1

Aquest plànol no pot ser reproduit ni cedit a tercers

sense l'autorització de la Fundació CIM

Xapa alumini 3mm de gruix

Tots els inserts cap a l'interior de
l'estructura menys el nº 9 (FH-M5-8)
que va cap a fora

Inici de tall
Pulir rebava

Inserts cap a fora

Toleràncies dimensionals generals segons DIN 7168-M | Toleràncies geomètriques generals segons DIN 7168 | Rugositat mínima general Ra=6.3 | Arxius adjunts: 040M01C01.0P01I Top frame.SLDPRT

Referència BCN3DSigma-M01C01.0P01I | Projecte: Sigmax Mòdul: Structure Conjunt: Main Structure

Escala 1:5 | Dissenyat Eric Pallarés | Dibuixat Mikel Ucero

Hoja / Total 1/1 | Comprovat Fabio Palmini | Aprovat Eric Pallarés | Versió plànol V1.0 | Contacte Fabio Palmini 93 413 76 68

Format de full A3

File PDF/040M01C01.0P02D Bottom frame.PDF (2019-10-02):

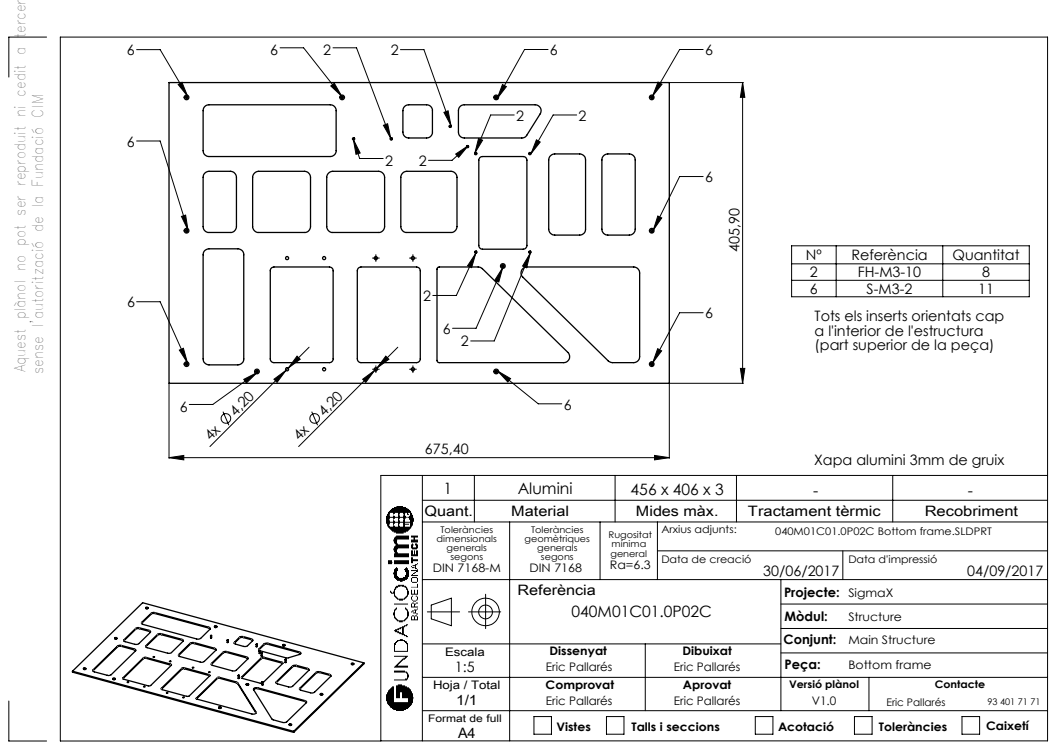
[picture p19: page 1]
Mides màx.; Tractament tèrmic; Recobriment; Data de creació; Data d'impressió; Vistes; Talls i seccions; Acotació; Toleràncies; Caixetí; Bottom frame

Aquest plànol no pot ser reproduit ni cedit a tercers

sense l'autorització de la Fundació CIM

Nº | Referència | Quantitat
2 | FH-M3-10 | 8
6 | S-M3-2 | 11

Tots els inserts orientats cap
a l'interior de l'estructura
(part superior de la peça)

Xapa alumini 3mm de gruix

Toleràncies dimensionals generals segons DIN 7168-M | Toleràncies geomètriques generals segons DIN 7168 | Rugositat mínima general Ra=6.3 | Arxius adjunts: 040M01C01.0P02C Bottom frame.SLDPRT

Referència 040M01C01.0P02C | Projecte: SigmaX Mòdul: Structure Conjunt: Main Structure

Escala 1:5 | Dissenyat Eric Pallarés | Dibuixat Eric Pallarés

Hoja / Total 1/1 | Comprovat Eric Pallarés | Aprovat Eric Pallarés | Versió plànol V1.0 | Contacte Eric Pallarés 93 401 71 71

Format de full A4

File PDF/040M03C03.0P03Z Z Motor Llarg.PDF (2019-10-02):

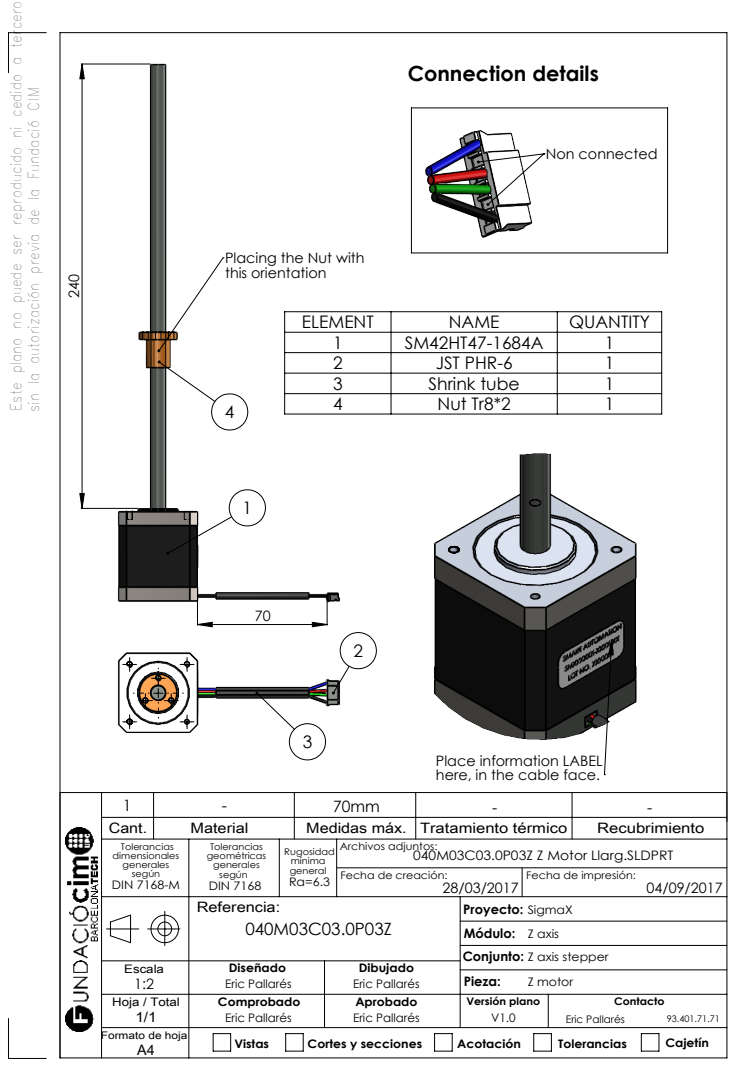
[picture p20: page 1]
Medidas máx.; Tratamiento térmico; Recubrimiento; Fecha de creación:; Fecha de impresión:; Vistas; Cortes y secciones; Acotación; Tolerancias; Cajetín; Z motor; Non connected; Connection details; ELEMENT; NAME; QUANTITY 1; JST PHR-6; Shrink tube; Nut Tr8*2

Este plano no puede ser reproducido ni cedido a terceros

sin la autorización previa de la Fundació CIM

Placing the Nut with
this orientation

Place information LABEL
here, in the cable face.

Tolerancias dimensionales generales según DIN 7168-M | Tolerancias geométricas generales según DIN 7168 | Rugosidad mínima general Ra=6.3 | Archivos adjuntos: 040M03C03.0P03Z Z Motor Llarg.SLDPRT

Referencia: 040M03C03.0P03Z | Proyecto: SigmaX Módulo: Z axis Conjunto: Z axis stepper

Escala 1:2 | Diseñado Eric Pallarés | Dibujado Eric Pallarés

Hoja / Total 1/1 | Comprobado Eric Pallarés | Aprobado Eric Pallarés | Versión plano V1.0 | Contacto Eric Pallarés 93.401.71.71

Formato de hoja A4

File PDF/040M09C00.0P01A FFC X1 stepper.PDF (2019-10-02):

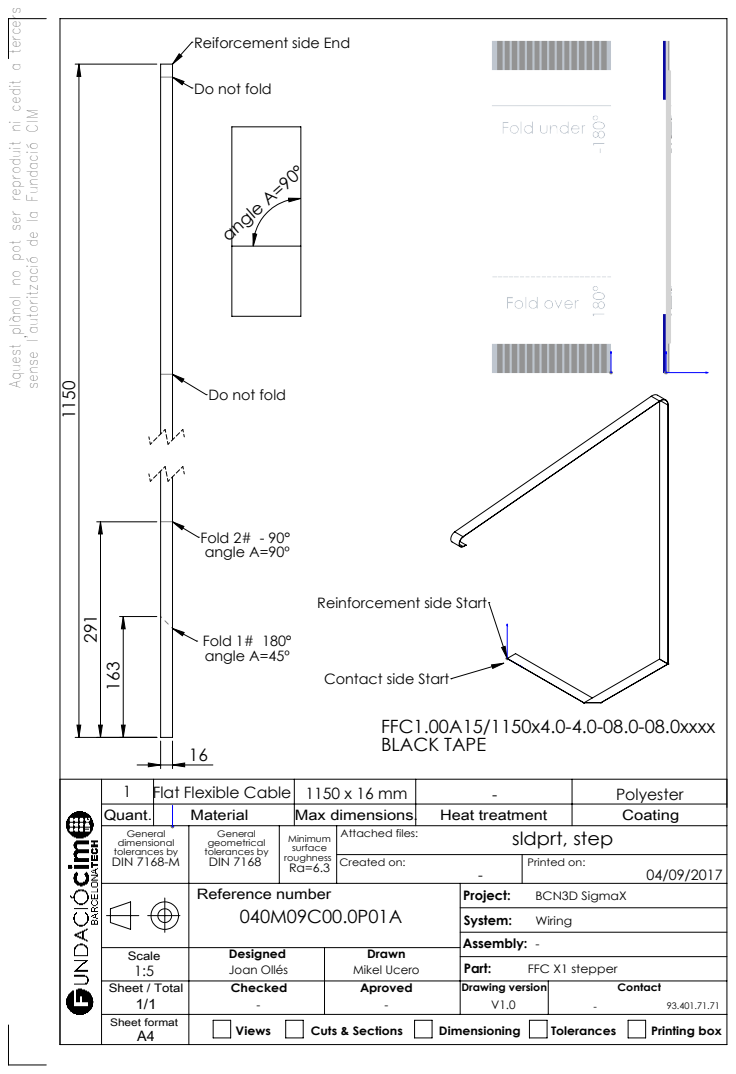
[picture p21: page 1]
angle A=90°; Max dimensions.; Heat treatment; Coating; Created on:; Printed on:; Views; Cuts & Sections; Dimensioning; Tolerances; Printing box; Flat Flexible Cable; FFC X1 stepper; Polyester; Fold 2# - 90° angle A=90º; Fold 1# 180° angle A=45º

Aquest plànol no pot ser reproduit ni cedit a tercers

Reiforcement side End

Do not fold

sense l'autorització de la Fundació CIM

Reinforcement side Start

Contact side Start
FFC1.00A15/1150x4.0-4.0-08.0-08.0xxxx
BLACK TAPE

General dimensional tolerances by DIN 7168-M | General geometrical tolerances by DIN 7168 | Minimum surface roughness Ra=6.3 | Attached files: sldprt, step

Reference number 040M09C00.0P01A | Project: BCN3D SigmaX System: Wiring Assembly: -

Scale 1:5 | Designed Joan Ollés | Drawn Mikel Ucero

Sheet / Total 1/1 | Checked - - | Aproved | Drawing version V1.0 | Contact -93.401.71.71

Sheet format A4

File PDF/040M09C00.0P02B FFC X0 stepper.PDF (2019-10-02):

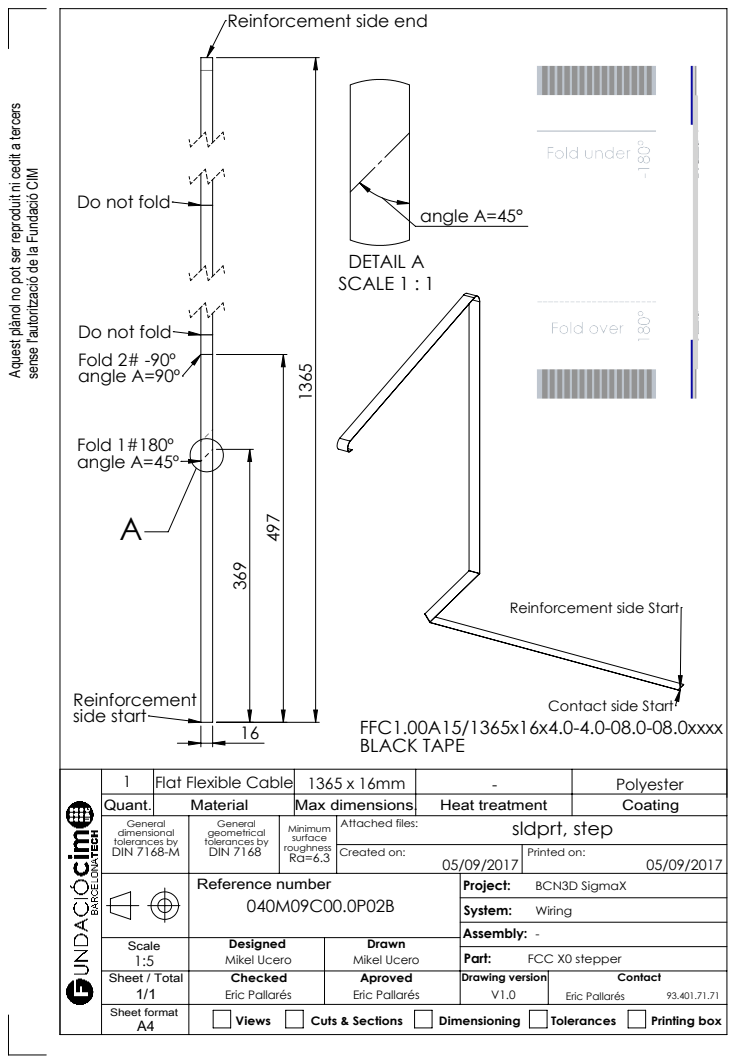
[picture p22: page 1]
Max dimensions.; Heat treatment; Coating; Created on:; Printed on:; Views; Cuts & Sections; Dimensioning; Tolerances; Printing box; FCC X0 stepper; Polyester; Fold 1#180º angle A=45º; side start; BLACK TAPE; angle A=45°; DETAIL A SCALE 1 : 1

Reinforcement side end

Aquest plànol no pot ser reproduit ni cedit a tercers

sense l'autorització de la Fundació CIM
Do not fold

Fold 2# -90º
angle A=90º

Reinforcement side Start

Contact side Start

Flat Flexible Cable
Quant.

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

Reference number 040M09C00.0P02B | Project: BCN3D SigmaX System: Wiring Assembly: -

Scale 1:5 | Designed Mikel Ucero | Drawn Mikel Ucero

Sheet / Total 1/1 | Checked Eric Pallarés | Aproved Eric Pallarés | Drawing version V1.0 | Contact Eric Pallarés 93.401.71.71

Sheet format A4

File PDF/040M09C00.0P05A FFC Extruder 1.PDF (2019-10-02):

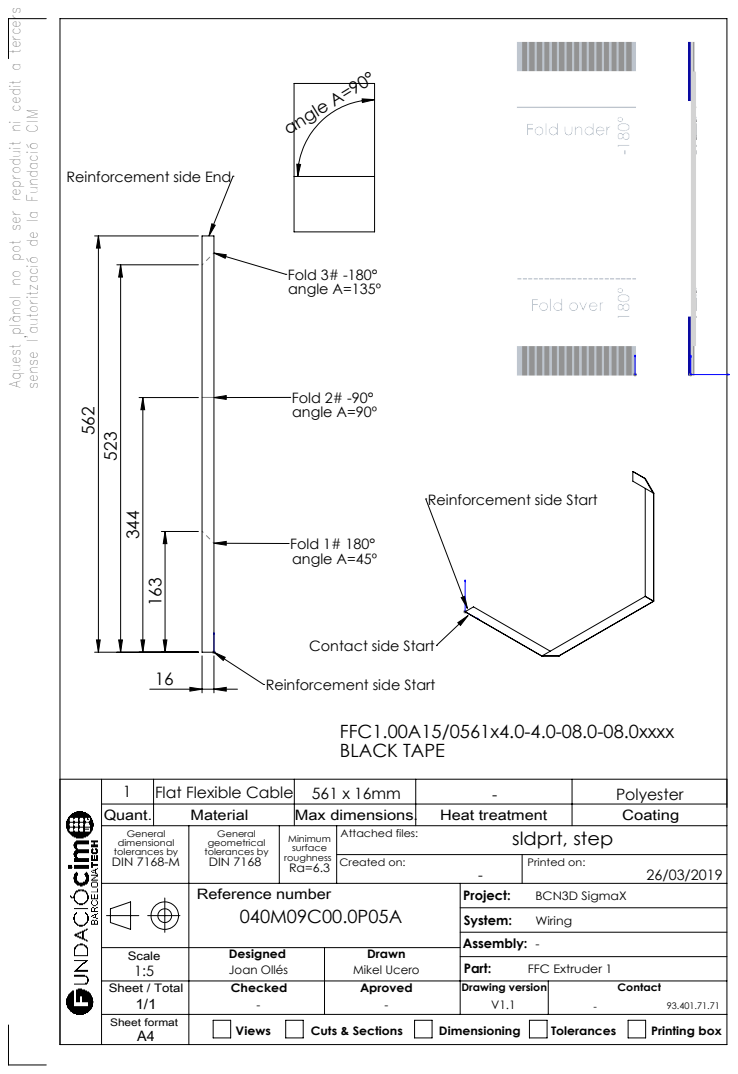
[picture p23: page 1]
angle A=90°; Max dimensions.; Heat treatment; Coating; Created on:; Printed on:; Views; Cuts & Sections; Dimensioning; Tolerances; Printing box; FFC Extruder 1; Polyester 163 344; Fold 1# 180° angle A=45º; Fold 2# -90° angle A=90º; Fold 3# -180° angle A=135º

Aquest plànol no pot ser reproduit ni cedit a tercers

sense l'autorització de la Fundació CIM

Reinforcement side End

Reinforcement side Start

Contact side Start

FFC1.00A15/0561x4.0-4.0-08.0-08.0xxxx
BLACK TAPE

Flat Flexible Cable
Quant.

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

Reference number 040M09C00.0P05A | Project: BCN3D SigmaX System: Wiring Assembly: -

Scale 1:5 | Designed Joan Ollés | Drawn Mikel Ucero

Sheet / Total 1/1 | Checked - - | Aproved | Drawing version V1.1 | Contact -93.401.71.71

Sheet format A4

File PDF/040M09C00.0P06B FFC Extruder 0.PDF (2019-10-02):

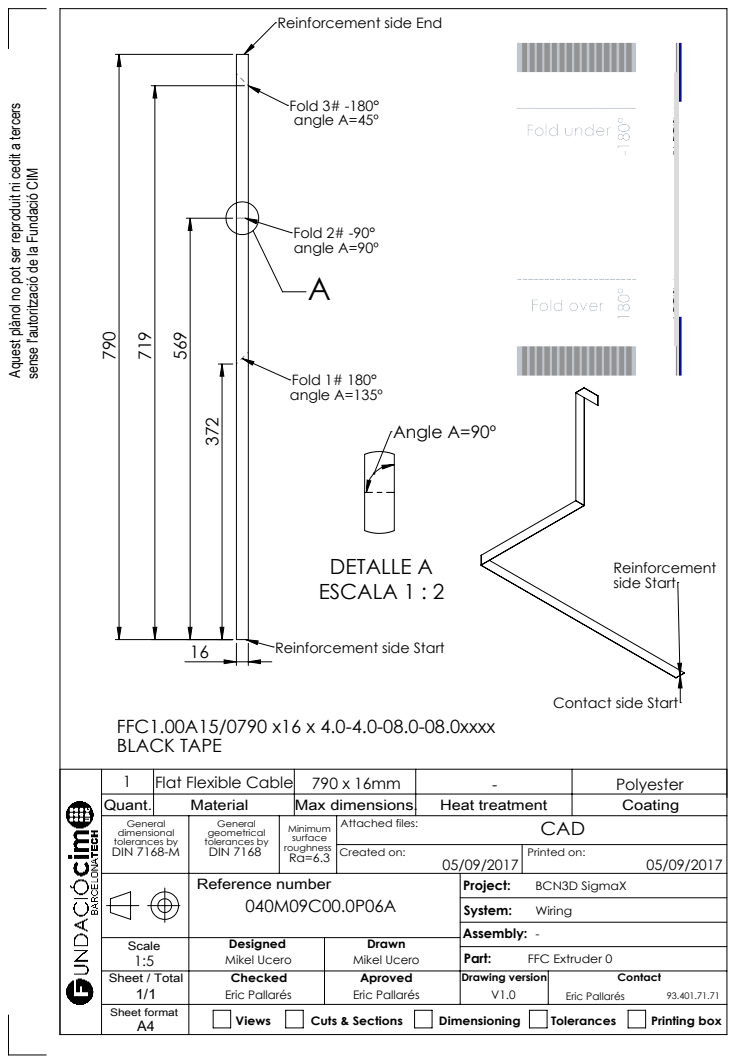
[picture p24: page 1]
Max dimensions.; Heat treatment; Coating; Created on:; Printed on:; Views; Cuts & Sections; Dimensioning; Tolerances; Printing box; FFC Extruder 0; Polyester; Fold 3# -180° angle A=45º; Fold 2# -90° angle A=90º; Fold 1# 180° angle A=135º; side Start; DETALLE A ESCALA 1 : 2; Angle A=90º

Reinforcement side End

Aquest plànol no pot ser reproduit ni cedit a tercers

sense l'autorització de la Fundació CIM

Reinforcement side Start

Contact side Start

FFC1.00A15/0790 x16 x 4.0-4.0-08.0-08.0xxxx
BLACK TAPE
Flat Flexible Cable
Quant.

General dimensional tolerances by DIN 7168-M | General geometrical tolerances by DIN 7168 | Minimum surface roughness Ra=6.3 | Attached files: | CAD

Reference number 040M09C00.0P06A | Project: BCN3D SigmaX System: Wiring Assembly: -

Scale 1:5 | Designed Mikel Ucero | Drawn Mikel Ucero

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

Sheet format A4

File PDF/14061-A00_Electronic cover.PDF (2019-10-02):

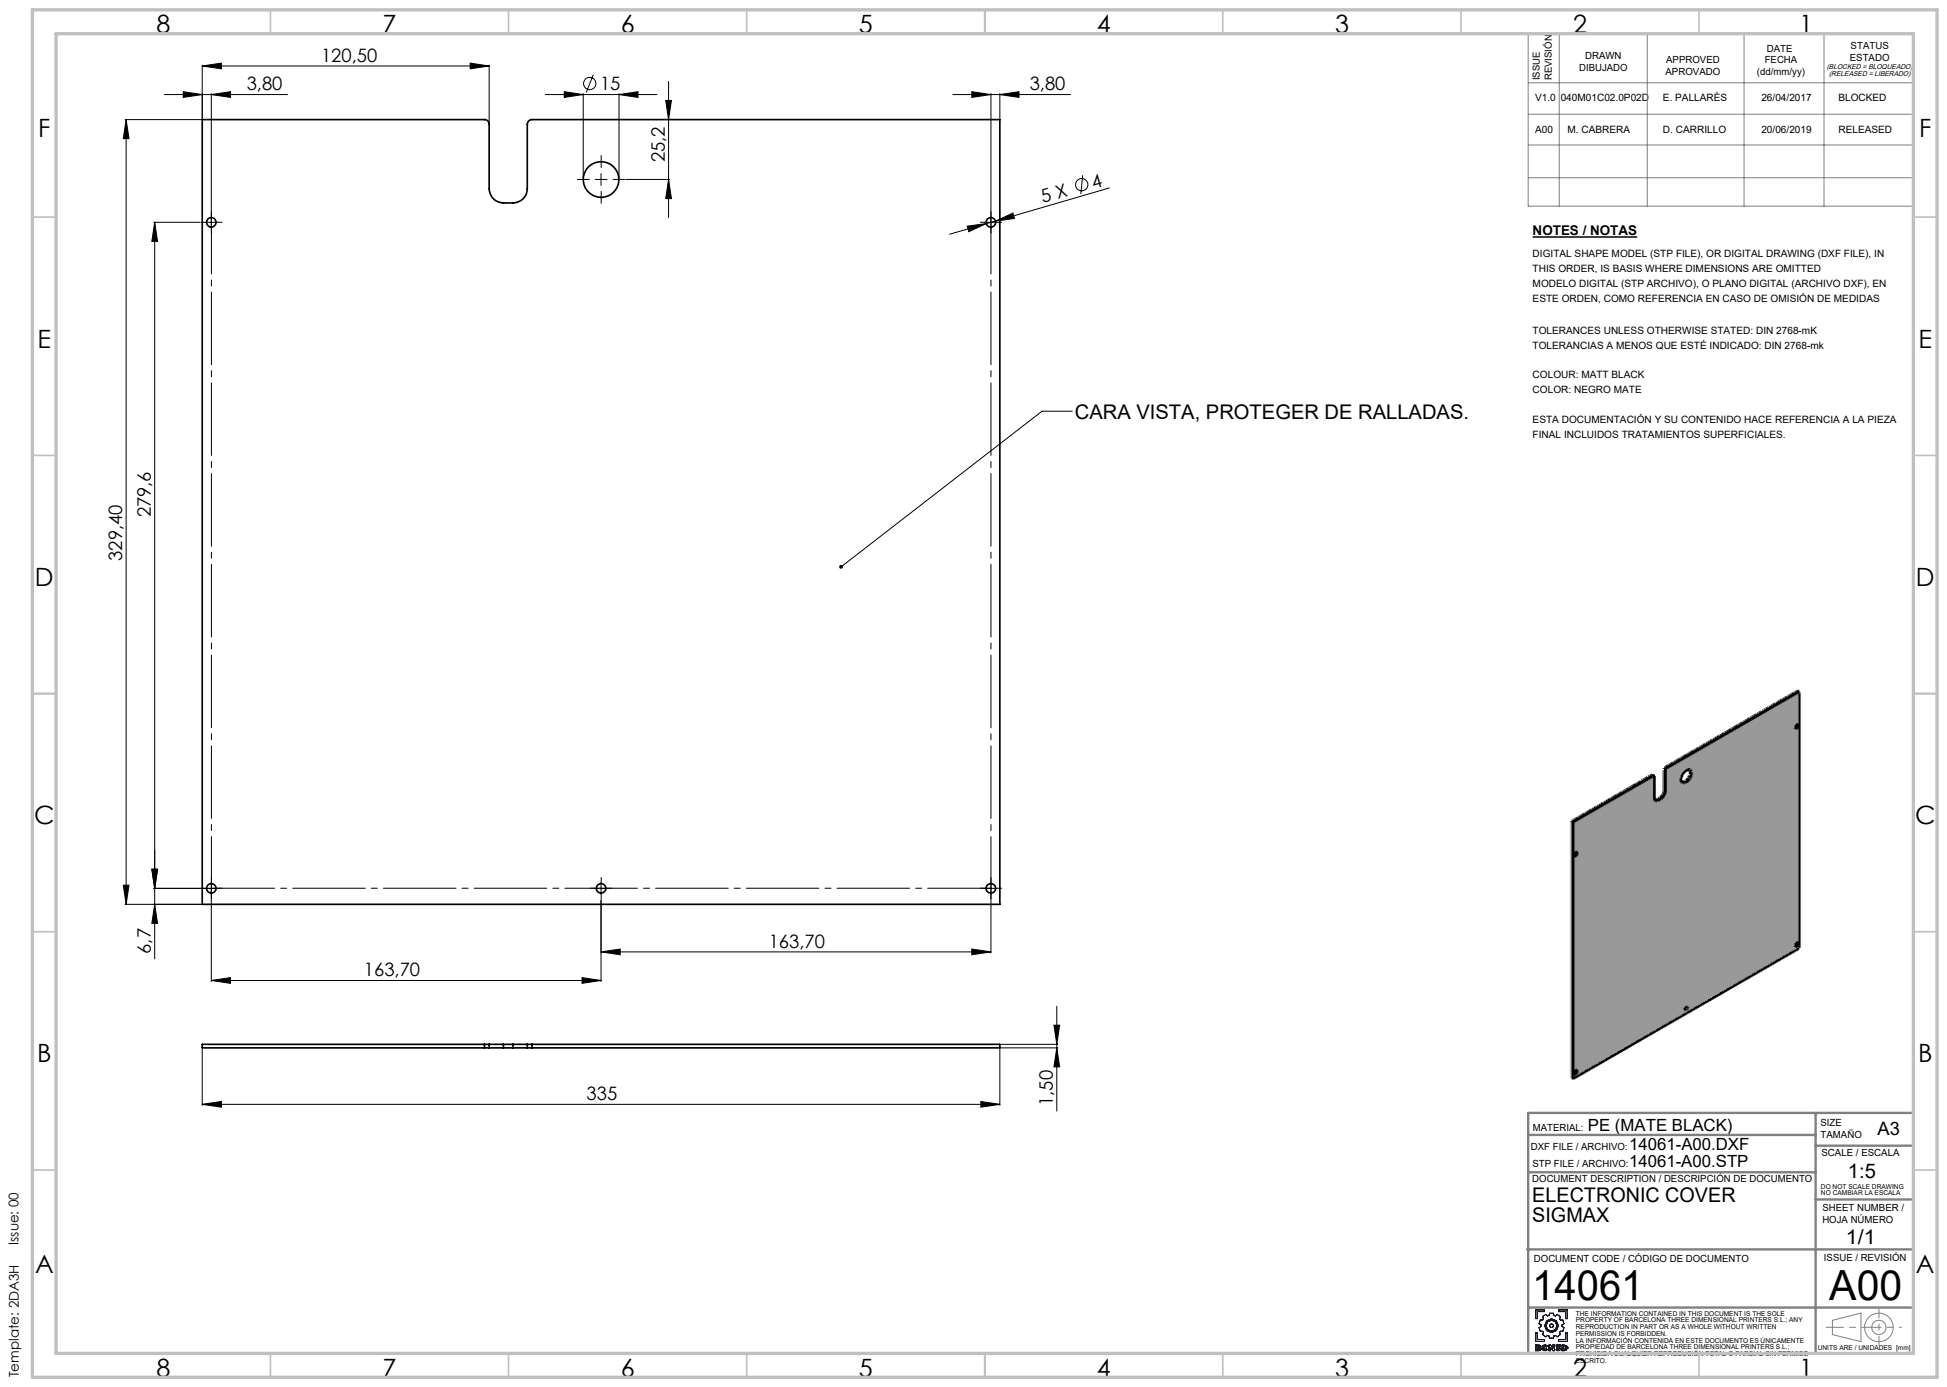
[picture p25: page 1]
SCALE / ESCALA; NOTES / NOTAS; Template: 2DA3H Issue: 00

120,50 | | DRAWN DIBUJADO | APPROVED APROVADO | DATE FECHA (dd/mm/yy) | STATUS ESTADO (BLOCKED = BLOQUEADO) (RELEASED = LIBERADO)

V1.0 | 040M01C02.0P02D | E. PALLARÈS | 26/04/2017 | BLOCKED

A00 | M. CABRERA | D. CARRILLO | 20/06/2019 | RELEASED

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

TOLERANCES UNLESS OTHERWISE STATED: DIN 2768-mK
TOLERANCIAS A MENOS QUE ESTÉ INDICADO: DIN 2768-mk

COLOUR: MATT BLACK
COLOR: NEGRO MATE

CARA VISTA, PROTEGER DE RALLADAS.

ESTA DOCUMENTACIÓN Y SU CONTENIDO HACE REFERENCIA A LA PIEZA
FINAL INCLUIDOS TRATAMIENTOS SUPERFICIALES.

MATERIAL:
DXF FILE / ARCHIVO:
STP FILE / ARCHIVO:
DOCUMENT DESCRIPTION / DESCRIPCIÓN DE DOCUMENTO
ELECTRONIC COVER
SIGMAX

PE (MATE BLACK)
14061-A00.DXF
14061-A00.STP

DO NOT SCALE DRAWING
NO CAMBIAR LA ESCALA
SHEET NUMBER /
HOJA NÚMERO

DOCUMENT CODE / CÓDIGO DE DOCUMENTO 14061 | ISSUE / REVISIÓN A00

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

PROHIBIDA CUALQUIER REPRODUCIÓN TOTAL O PARCIAL SIN PERMISO
ESCRITO.

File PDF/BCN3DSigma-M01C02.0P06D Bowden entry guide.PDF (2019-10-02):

Mides màx.; Tractament tèrmic; Recobriment; Data de creació; Data d'impressió; Vistes; Talls i seccions; Acotació; Toleràncies; Caixetí; PLA negre

Aquest plànol no pot ser reproduit ni cedit a tercers

sense l'autorització de la Fundació CIM

INFILL | LAYER HEIGHT | SHELL THICKNESS | BOTTOM/TOP THICKNESS
100% | 0.15 mm | 2 | 3

Toleràncies dimensionals generals segons DIN 7168-M | Toleràncies geomètriques generals segons DIN 7168 | Rugositat mínima general Ra=6.3 | Arxius adjunts: BCN3DSigma-M01C02.0P06D Bowden entry guide.stl

Referència BCN3DSigma-M01C02.0P06D | Projecte: BCN3DSigma Mòdul: Structure Conjunt: Structure covers

Escala 2:1 | Dissenyat Bernat Poll | Dibuixat Eric Pallarés

Bowden entry guide

Hoja / Total 1/1 | Comprovat Bernat Poll | Aprovat Bernat Poll | Versió plànol V1.0 | Contacte Bernat Poll 93.401.71.71

Format de full A4

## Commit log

2019-10-07 change folder name
    [040M01C00.0P000 Structure.SLDASM, 040M01C01.0P02E (Test) Bottom frame.SLDPRT, 040M01C01.0P11Z Power button.SLDPRT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]
2019-10-15 rev 0.1
    [040M01C00.0P000 Structure.SLDASM, 040M01C01.0P02E (Test) Bottom frame.SLDPRT, 040M01C01.0P11Z Power button.SLDPRT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]
